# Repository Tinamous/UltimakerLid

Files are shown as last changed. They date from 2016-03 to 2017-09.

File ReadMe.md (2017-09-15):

#Ultimaker 2 Lid.

An acrylic lid for the Ultimaker 2, 2+ and Extended to help keep dust off the printer bead and maintain a more stable thermal environment.

#### V1.1 Lid:

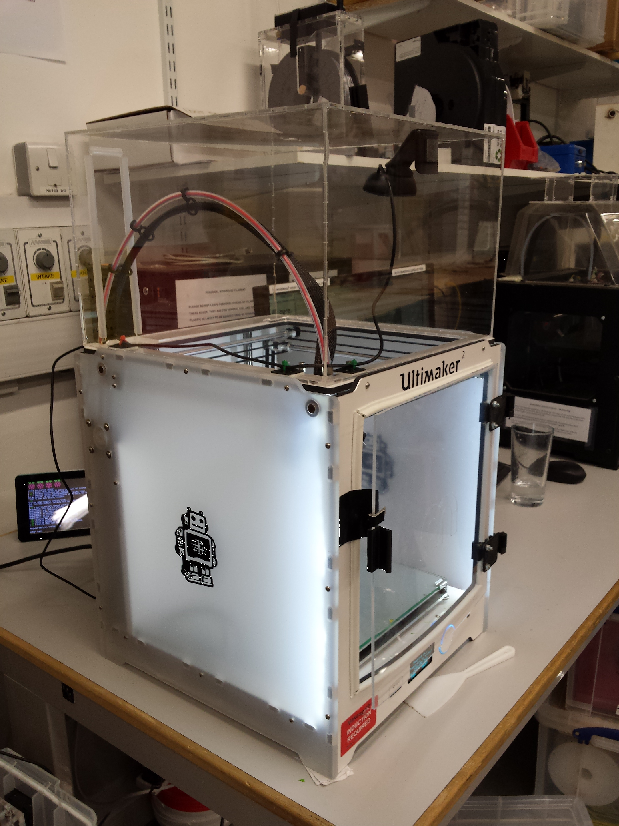
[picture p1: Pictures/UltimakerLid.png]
Ultimaker 2 Lid V1.1


#### V1.2 Lid:

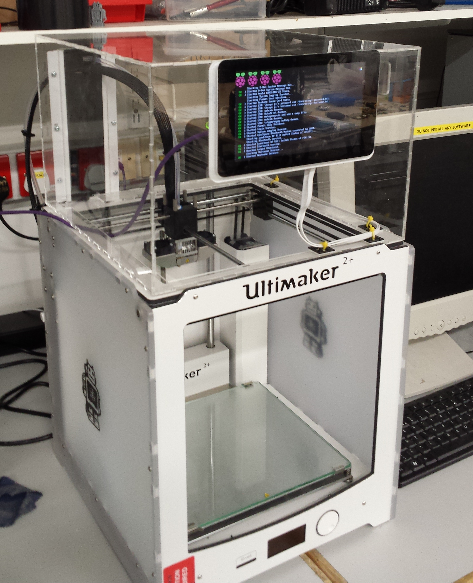
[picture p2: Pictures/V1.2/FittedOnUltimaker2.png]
Ultimaker 2 Lid V1.2


* Use 3mm Acrylic.
  * Use clear if you want to see your print when the lid is fitted
  * Suggest using cast acrylic to reduce internal forces in sheets.
* Laser cutting guides are for 600x400 sheets.
* Use Tensol 12 glue to glue the lid together.

### Versions:

* V1.0: Initial version - ignore this.
* V1.1: First built version. Option for hole in the top to allow mounting of camera.
* V1.2: Features a larger opening at the back to allow 2x draft excluder brush sets to be added and an opening at the front for the Raspberry Pi 7" Touch screen.
* V1.2.1: Do no use - Builds on V1.2 but is 40mm higher which makes better use of the acrylic when in 600x400 sheets. Appears Pi Display design changed.
* V1.2.2: Builds on V1.2.1 with better cutout for Pi Display, 40mm fan for pi cooling, 80 or 120mm fan cutouts at back.

V1.2.2 is the best option. However if you don't want the Pi Display mount on the front remove this in Inkscape or the laser cutter software.

Draft excluder used is Wickes "Brush Draught Excluder" - White PVCu. Product Id:218004 (http://www.wickes.co.uk/Wickes-Door-Brush-Draught-Excluder-White-838mm/p/218004)

V1.1 has a smaller opening for the Ultimaker boden tube and cables, if you don't want to use the draft excluder this version is better. Use the base of V1.1 as well as the opening is a different size.

If you don't use the draft excluded version cover the sharp edges where the boden tube goes through to prevent damadge. Some 6-8mm pipe the of the same material used for the boden tube, split along the length makes for a great cover.

### Lid Size: 

Width: 322mm
Height: 220mm (240mm for V1.2.1 and V1.2.2)
Depth: 335mm

## Assembly:

Glue: Use Tensol 12. http://www.rapidonline.com/pdf/87-2330U.PDF

Glue only in a well ventilated area. Don't spend too long in the area. 

Store the glue in the fridge for 24 hours before use and keep refrigerated between use, this increases the viscosity of the glue and makes it easier to work with.

The lid is glued in 4 stages with a 3 hour gap between each stage to allow the glue to set.

Black electrical tape is used to hold the box together when gluing, this works well as it's easily removed and can be stretched over corners to help keep the joints tight.

### Prep:

* You may wish to anneal the acrylic first to reduce the risk of cracking when glued. (See: https://en.wikipedia.org/wiki/Poly(methyl_methacrylate))
  * If using cast acrylic this may not be such an issue as the inner forces of the acrylic are less.
* Cut ~32 x 4-6 inch pieces of electrical tape ready to hold the box panels in place.
* Remove the all protective covering off all the pieces, you don't want that glued into your lid.
* Ensure you have a clean flat working surface and kitchen towel or similar to wipe up any dripped glue.
* Glue will run through the lid joints onto the work bench. Working on a paper cover will result in the paper being stuck to the lid, use wood as the work top (suggest not kitchen work top!)

When gluing:

* Don't apply too much glue.
* A 1-2mm bead size is ample. This will get drawn into the joint and give a high glue surface area.
* Try to get glue only where it is needed otherwise it eats into the finished surface and looks horrible. (i.e. don't dribble)
* Don't let the glue dispenser warm to much as the glue becomes very runny and is difficult to work with very quickly. Always return the glue to the fridge.
* You may wish to move the lid slightly every now and then shortly after gluing to remove any excess glue of the surface the lid is sitting on. Don't wipe the lid through as this will smear glue over it and look horrible.

### Assembly:

#### Phase 1 - Glue the bottom on:

* Place the lid base (the piece with the large hole in from sheet 3) on a flat surface with the back opening at the back left as it would be when fitted on the printer.
* Put 2 pieces of electrical tape on the bottom of the base piece on each side coming out about 3 inches ready to connect to a side/front/back panel.
* Place the back panel on ensuring the large hole matches up with the cut out on the base and is on the left hand side. This allows the cable/boden tube to go through the lid into the ultimaker. 
* Pull the tape tight and press against the back panel.
* Place a side panel onto one side, hold in place with the tape from the base, also add 2 pieces of tape along the back panel to side panel edge to hold them tight
* Repeat for the other side.
* Repeat for the front panel ensuring the cutout for the Pi Display is at the top, finally taping the front panel to the two side panels.
* The box should now be in a good shape and look almost as it would sat on the printer, held together sturdily with the electrical tape. Do not fit the lid yet
* Run a bead of Tensol 12 glue along the connecting 4 edges of the base (front/back and sides). 
* Do not glue up the edges at this stage as the glue will run down and form a big blob in the corner.
* Fit the top now to ensure the whole thing is square whist the glue sets. Ensure there is no glue around the top so it doesn't stick.
* Return glue bottle to fridge.
* Put kettle on and make a nice cup of tea.
* Wait for 3 hours for the glue to set.

#### Phase 2 - Glue one side:

* Rotate the lid 180 degrees so the back panel is nearest to you.
* Flip forwards so the top is now facing you and the back panel is laying flat on the bench.
* Remove the top.
* Run a bead of glue along both the mating edges of the back and side panels (should be horizontal on the bench now). 
  * Run the glue from the furthest away point stopping 20mm before getting to the lid top (i.e. going from lid bottom to top)
  * Be sure not to glue all the way to the lid top to prevent risk of gluing the top on at this stage.
* Return glue bottle to fridge. 
* Provided there is no glue near the lid connection you may wish to put the lid on to help keep the box square, suggest waiting a bit to let the glue spread first to ensure it won't creep into the top of the lid.
* Put kettle on and make a nice cup of tea.
* Wait for 3 hours for the glue to set.

#### Phase 3 - Glue the other side:

* Rotate the box 180 degrees so the last glued edge is now in the air and the remaining two side unglued edged are flat on the bench. Remove the lid if fitted.
* Repeat gluing as above, run a bead of glue from the back to the front along the side edges stopping 20 mm before the lid.
* Return glue bottle to fridge and again wait for the glue to start to set so it is no longer moving and fit the lid if you wish.
* Put kettle on and make a nice cup of tea.
* Wait for 3 hours to allow glue to set.

#### Phase 4 - Glue the top:

* Ensure that the top if fitted squarely, add some electrical tape top hold it in place against the sides/back/front.
* Rotate the lid forward so the lid top is now flat on the bench.
* You can now glue the 4 edges of the top to the sides/front/back panels by putting your hand through the large hole in the base panel.
  * Don't tilt the glue bottle when doing this otherwise you'll get glue on the inside of the lid top. Tilt the bottle only when about to glue the edges.
* Return glue bottle to fridge and wait 3 hours for the glue to set.
* Remove the electrical tape.
* Put kettle on and make a nice cup of tea you certainly deserve one now!

The glue should fully harden in 3 weeks, however it is usable once the final 3 hour wait is over. 

Hardening to reduce the 3 weeks can be speeded up by heating AFTER 24 hours, refer to the glue instructions for details on this.

#### Phase 5:

##### Draft excluder brushes

* Cut 2 lengths of draft excluder brush to fit the rear gap. 
  * Try to cut it so that one of the holes in the draft excluder lines up with a hole in the acrylic otherwise it will look odd
  * The brush should sit on the outside of the back of the lid with the fat part sitting in the gap towards the inside of the lid, this provides protection against the sharp edges of the lid for the moving cables and boden tube
* Mark then drill the other 2 holes in each brush of the draft excluder.
* You may wish to crimp the lower end of each brush to stop the bristles coming out now it's been cut.
* Fit both brushes using M3 machine screws, bolts and washers.

##### 7" Pi Display

* Cut 2x outlines from 3mm acrylic for the display (see V1.2 files).
  * If using V1.2 this may well come out of the offcuts from the back and front panel and the base panel.
* Attach the Pi Display PCB onto the display and connect up the flex cables
* Attach the display PCB to Pi flex cable (do not connect to the Pi at this time)
* Attach the 5v & GND cables to the display PCB
* Plug the Micro USB cable into the display PCB
** If using a Pi 3 with WiFi the voltage drop on the USB cable may be to large so use 2x USB cables, one for the Pi and one for the display and link only the GND connection
* Fit the smaller acrylic display mount first to the display
* Fit the slightly larger one next (this gives a stepped impression around the bottom and sides of the display
  * Ensure the cut out on the inside is at the bottom where the flex cable is.
  * No need to glue these, they are held in place by the display.
* Offer the display to the front of the lid carefully feeding in the USB, and interconnect cables.
  * The display flex cables go at the bottom and the display pcb to pi interconnect flex on the right hand side.
* Mound the display to the lid using M3 machine screws and washers on the inside to spread the load of the forces (don't over tighten) - suggest nylon bolts.
* Mount the Pi onto the display as you would do normally.
* Run the power cable to the bottom of the lid and around the edge to the right and hold in place with sticky feet and cable ties (ensure it won't get snagged with the printer head).
* Take the USB cable out of the lid via the small hole at the back right (V1.2+ only)
* Don't fix the cable to the ultimaker as this will hinder you removing the lid.
* Optionally include Ethernet cable if you're not using Wi-Fi
* Optionally include a USB camera on the back of the lid to monitor the roll, run the USB cable for that with the power USB cable
* Optionally include a USB cable to go to the USB port on the Ultimaker
* Optionally include an internal USB camera. Mount this to the lid back/side/front/top as you like with sticky fixers.
* Optionally attach a Pi Camera and mount that as desired.
* Optionally attach a Pi Hat to light up or monitor the temperature/humidity inside the lid.
* Optionally run OctoPi/OctoPrint on the Pi (NB: This doesn't appear to work overly well with the printer, we use it only for webcam monitoring).

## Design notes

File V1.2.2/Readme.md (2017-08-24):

Same as V1.2.1 (Draft excluder at rear and Pi Display, 40mm higher to make better use of 600x400 acrylic sheet).

* Increased cutout for the Raspberry Pi Display as the fixings appear to have changed slightly and it was already tight to fit.
* Moved Pi display down a little
* Cutout in top for 40mm fan to cool Pi.
* Cutout at rear for 80 or 120mm fan to cool/filter printer environment
* Add hole for DC Power connector. (12mm)
* Bottom - added plates for fans to cover hole if required
* Bottom - reduced cutout for screw/boden cable exit so it doesn't cut through the back as well.

Right, Left are unchanged from V1.2.1

Use http://www.makercase.com/ to create laser cut plan from .json file.

40mm fan (Top)
--------------
Holes 32mm apart. (16 from center)
main hole 38mm

Use:
{"params":[161,309,37,1],"type":"roundHole"},
{"params":[145,293,4,2],"type":"roundHole"},
{"params":[145,325,4,3],"type":"roundHole"},
{"params":[177,325,4,4],"type":"roundHole"},
{"params":[177,293,4,5],"type":"roundHole"}

80mm fan (Back)
---------------
Holes 71mm apart. (35.5 from center)
main hole 75mm

Use:
{"params":[60,60,75,10],"type":"roundHole"},
{"params":[24.4,24.4,4.4,11],"type":"roundHole"},
{"params":[24.4,95.5,4.4,12],"type":"roundHole"},
{"params":[95.5,95.5,4.4,13],"type":"roundHole"},
{"params":[95.5,24.4,4.4,14],"type":"roundHole"}

Add also cutout on bottom to cover the hole if not in use.

120mm fan (Back)
----------------
Holes 105mm apart. (52.5 from center)
main hole 115mm

Use:
{"params":[80,80,115,15],"type":"roundHole"},
{"params":[27.5,27.5,4.4,16],"type":"roundHole"},
{"params":[27.5,132.5,4.4,17],"type":"roundHole"},
{"params":[132.5,132.5,4.4,18],"type":"roundHole"},
{"params":[132.5,27.5,4.4,19],"type":"roundHole"},

Add also cutout on bottom to cover the hole if not in use.

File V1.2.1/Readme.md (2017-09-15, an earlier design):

Do not use this design. It appears the Pi Display has changed slightly making the cutout not work well. V1.2.2 has a larger cutout and is down a little to give a better fit.

Same as V1.2 (Draft excluder at rear and Pi Display) but 40mm higher (to make better use of 600x400 acrylic sheet + give more stable zone at the top with lack of airflow

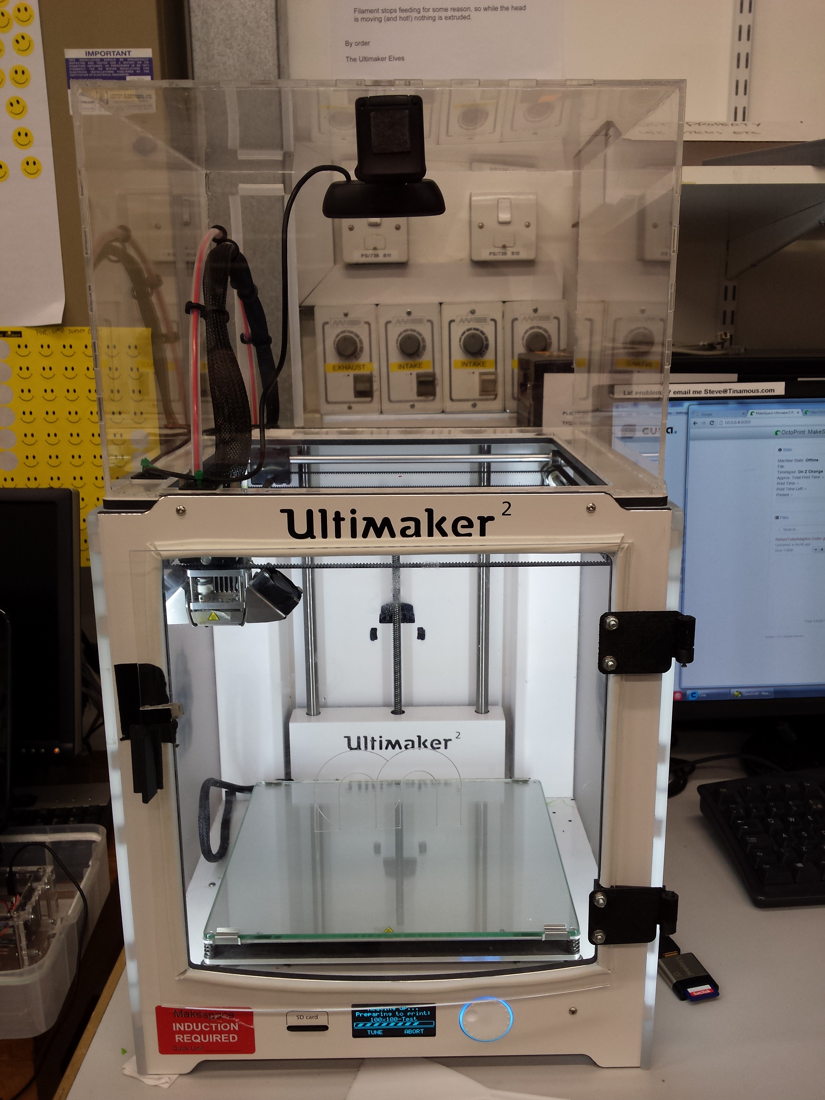
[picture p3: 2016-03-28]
Pictures/2015-11-13 16.56.00.jpg

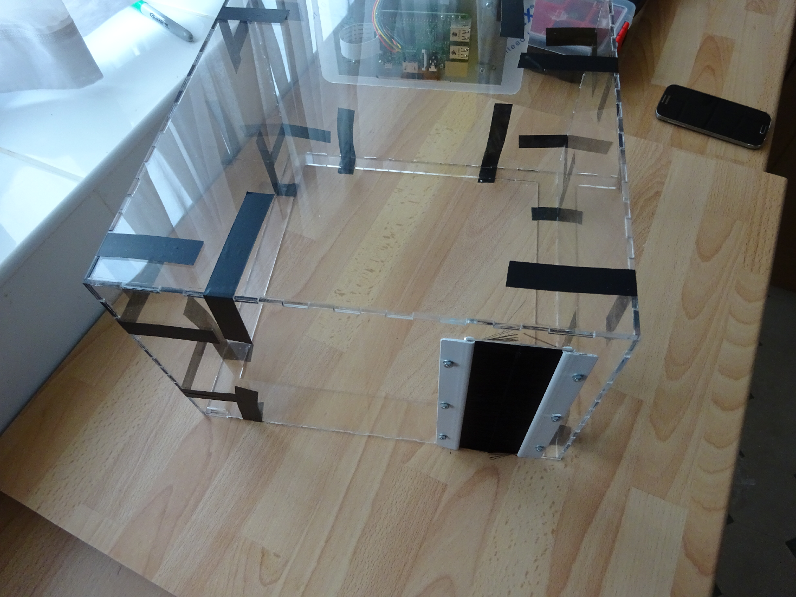
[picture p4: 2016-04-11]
Pictures/V1.2/RearBrushes.png

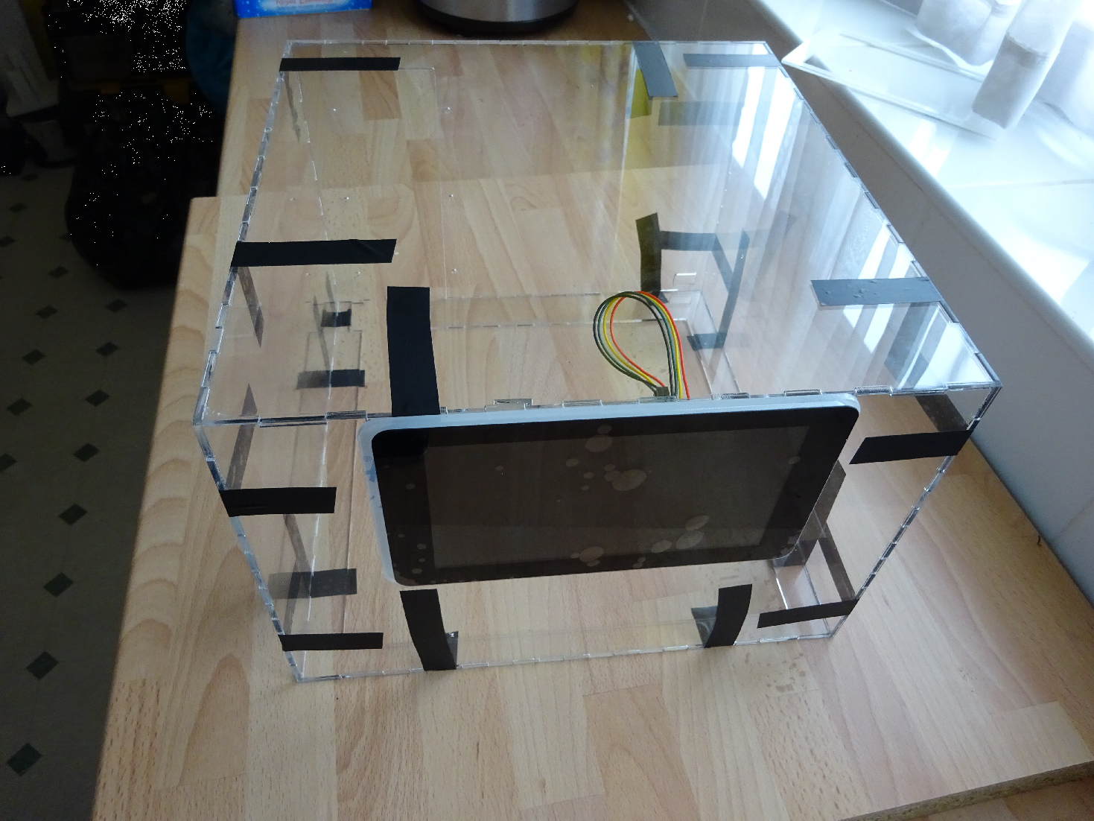
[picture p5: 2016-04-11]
Pictures/V1.2/PiDisplay.png

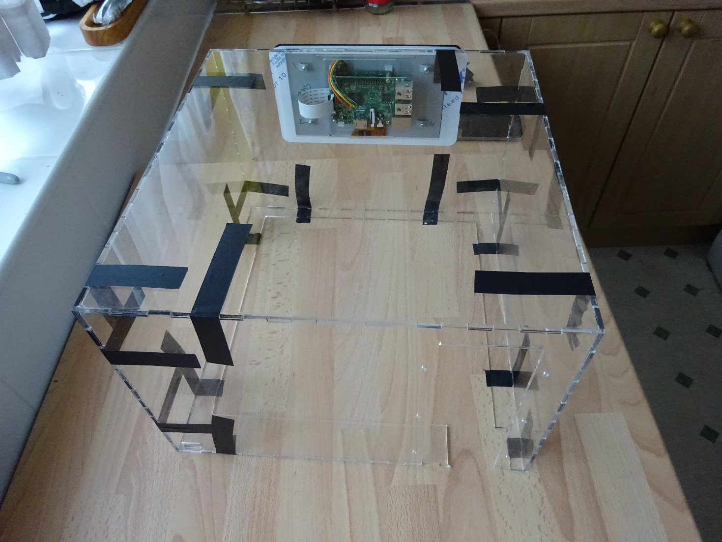
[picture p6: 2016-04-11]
Pictures/V1.2/PiDisplayRear.png

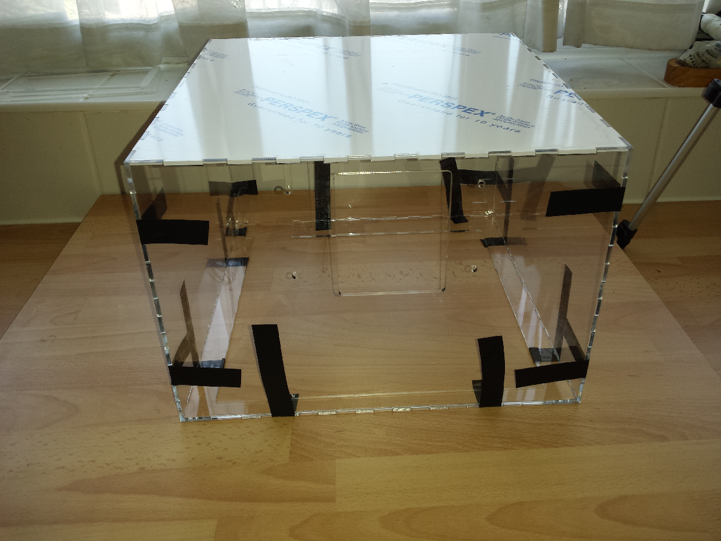
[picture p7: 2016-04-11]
Pictures/V1.2/GluingBase2.png

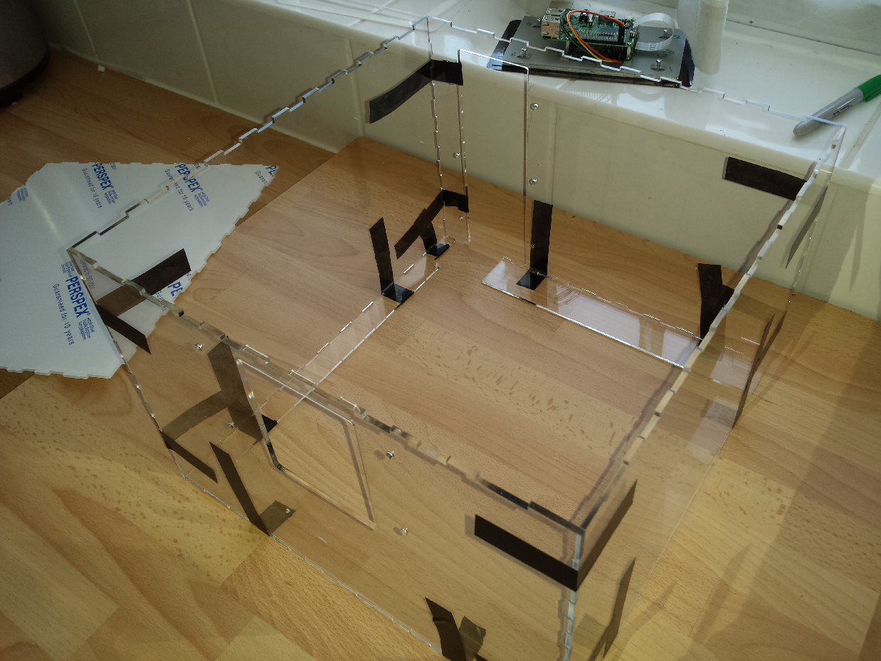
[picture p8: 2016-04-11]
Pictures/V1.2/GluingBase.png

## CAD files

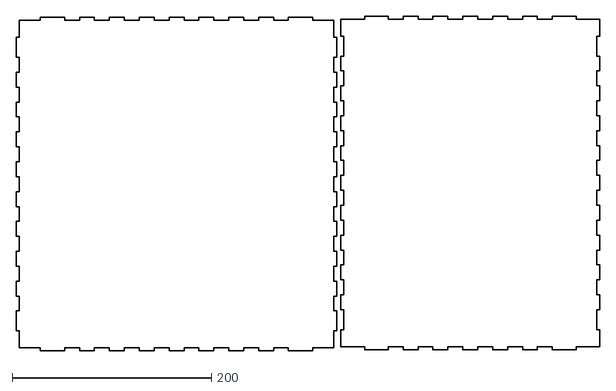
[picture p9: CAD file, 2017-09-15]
V1.2.2/TopAndSide-600x400-NoTopFan.dxf
586.2 x 336.2

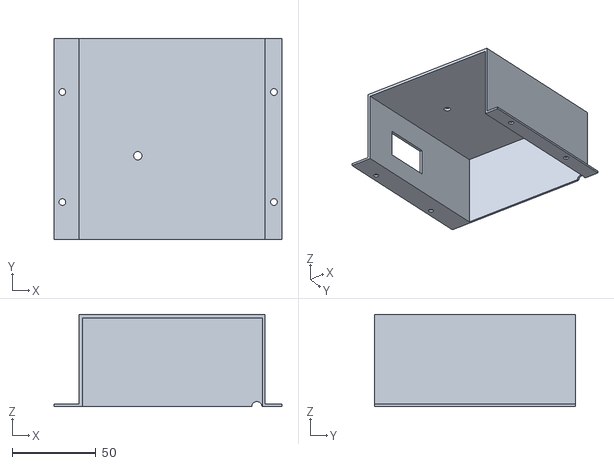
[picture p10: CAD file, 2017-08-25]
V1.2.2/PiCase.stl
136.0 x 120.0 x 55.0

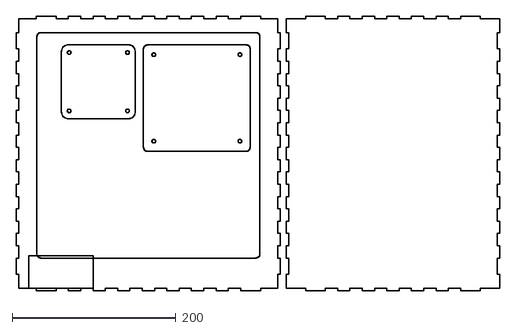
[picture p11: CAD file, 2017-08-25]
V1.2.2/BottomAndSide-600x400.dxf
589.3 x 335.0

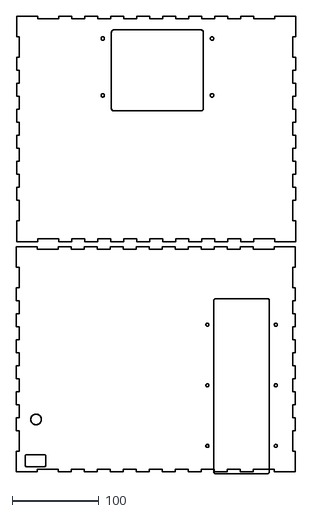
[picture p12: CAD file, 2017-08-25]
V1.2.2/BackAndFront-600x400-NoFan.dxf
322.3 x 528.0

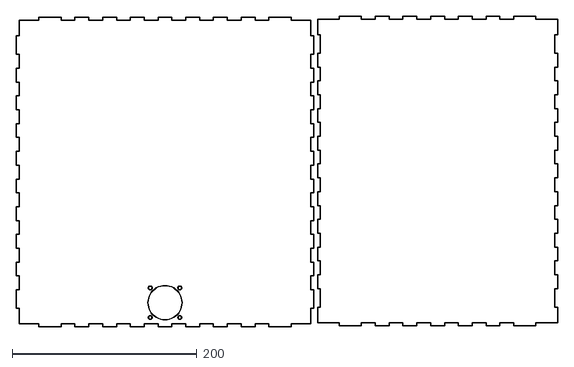
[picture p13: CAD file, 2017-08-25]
V1.2.2/TopAndSide-600x400.dxf
586.2 x 336.2

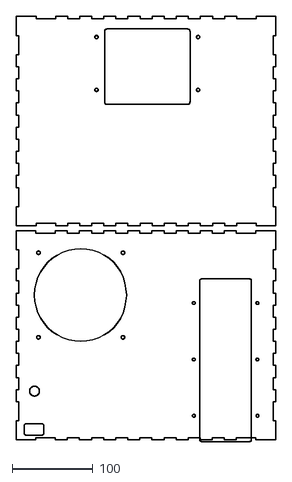
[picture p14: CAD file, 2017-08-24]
V1.2.2/BackAndFront-600x400-120Fan.dxf
322.3 x 528.0

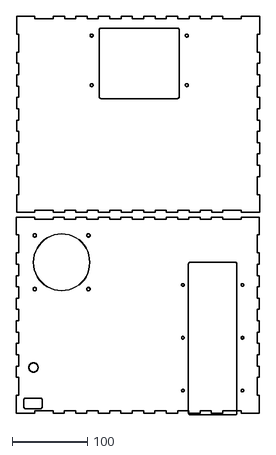
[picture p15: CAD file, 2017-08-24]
V1.2.2/BackAndFront-600x400-80Fan.dxf
322.3 x 528.0

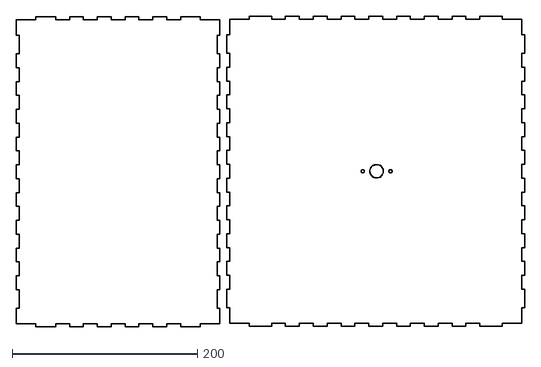
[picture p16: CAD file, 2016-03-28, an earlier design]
V1.1/lid-2b - TopWithCameraHoleAndSide.dxf
549.4 x 335.6

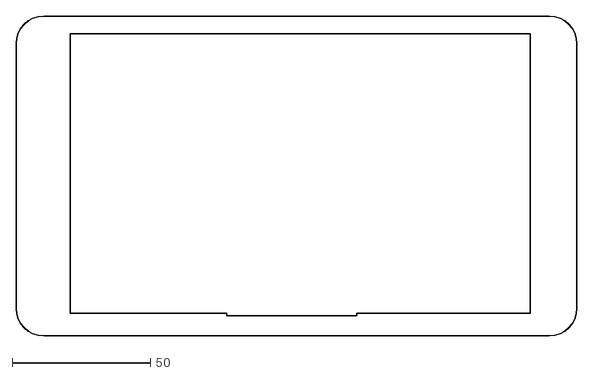
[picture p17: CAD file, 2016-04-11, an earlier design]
V1.2/DisplaySuround-2b.dxf
203.0 x 115.8

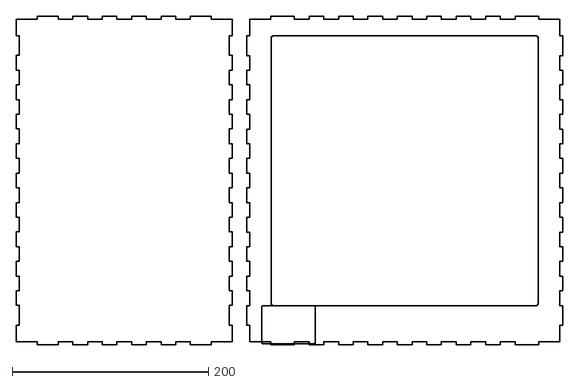
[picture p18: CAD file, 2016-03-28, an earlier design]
V1.1/lid-3 - BottomAndSide.dxf
556.9 x 335.1

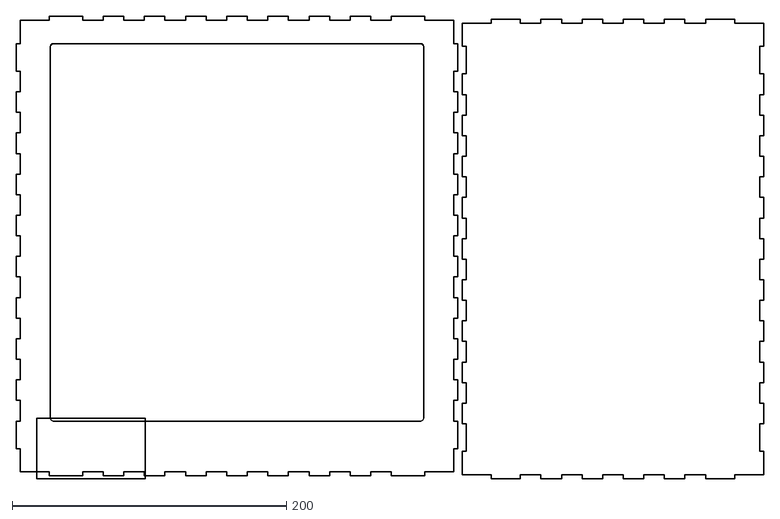
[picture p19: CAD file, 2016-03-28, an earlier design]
V1.2/BottomAndSide-600x400.dxf
545.0 x 337.0

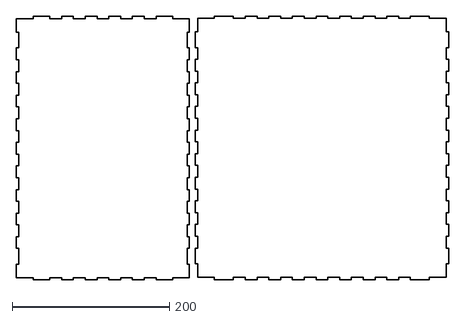
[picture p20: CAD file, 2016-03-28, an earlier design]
V1.1/lid-2a - TopNoHolesAndSide.dxf
549.4 x 335.6

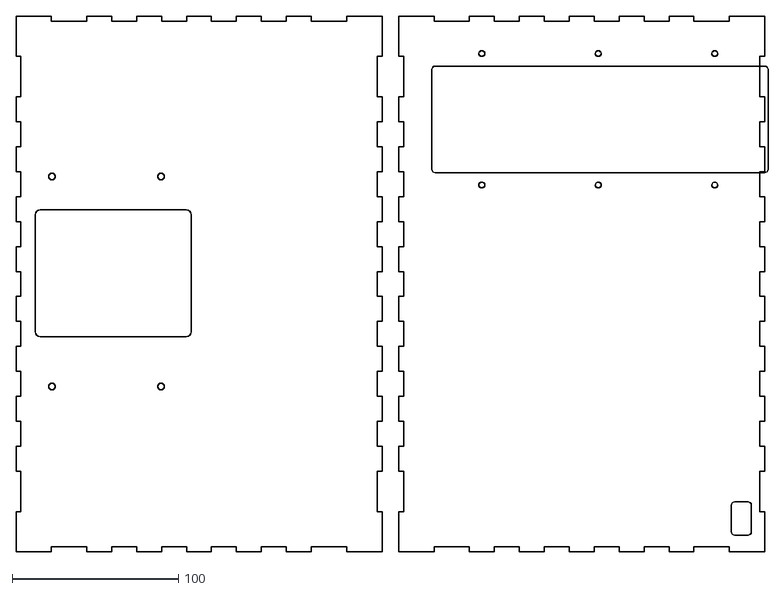
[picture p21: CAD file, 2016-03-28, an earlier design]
V1.2/BackAndFront-600x400.dxf
452.0 x 322.0

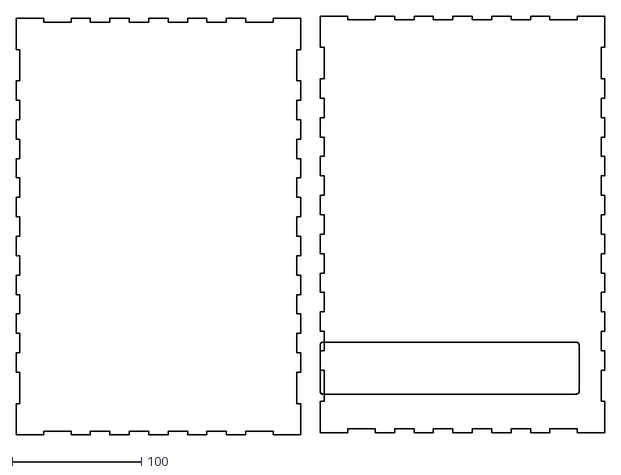
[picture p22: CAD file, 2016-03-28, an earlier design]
V1.1/lid-1 - BackAndFront.dxf
454.9 x 323.6

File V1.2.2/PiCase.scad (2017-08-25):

$fn = 60;

//{"params":[225.59,25.58,4,1],"type":"roundHole"},
//{"params":[225.59,91.23,4,2],"type":"roundHole"},
//{"params":[99.39,25.58,4,3],"type":"roundHole"},
//{"params":[99.39,91.23,4,4],"type":"roundHole"},
//{"params":[109.39,15.58,106.2,93.65,3,5],"type":"rectHole"}],

width = 136; // X
height = 120; // Y
depth = 55; // Z
// First hole y offset
// this is different between V1.2.1 and 1.2.2 cases
//holeYOffset = 21.58; // V1.2.1 - TODO: Check!
holeYOffset = 25.58; // V1.2.2

module PiModel() {
    translate([13+5, holeYOffset + 2, 13]) {
        cube([85, 60, 40]);
        
        // USB 
        translate([-20,0,1]) {
            cube([22,15, 18]);
        }
        
        // Second USB
        translate([-20,20,1]) {
            cube([22,15, 18]);
        }
        
        // Power connector
        translate([85,36,12]) {
            cube([15,12, 10]);
        }
    }
}

module baseLayer() {
    difference() {
        union() {
            // Base layer for holes.
            cube([width, height, 1.5]);
            
            translate([5 + 10, 0, -0]) {
                cube([width - 15 - 10, height, depth]);
            }
        }
        union() {
            // Drill the holess..
            // 5mm in, and 25.58mm down (from laser) - 3mm thickness acrylic + tollerance
            translate([5, holeYOffset- 3.2, -0.1]) {
                cylinder(d=4, h=2);
                translate([126.2, 0, 0]) {
                    #cylinder(d=4, h=2);
                }
                
                translate([126.2, 65.65, 0]) {
                    #cylinder(d=4, h=2);
                }
                
                translate([0, 65.65, 0]) {
                    #cylinder(d=4, h=2);
                }
            }
            
            // Cut out main Pi Body
            translate([5 + 12, -0.01, -0.1]) {
                cube([width - 17 - 11.5, height-1.5, depth-2]);
            }
            
            // Pi Offset (Y=0 = 27mm, X=13+5)
            // Cut out for the USB connectors
            translate([5 + 9 - 0.01, 26, 15]) {
                cube([4, 36, 20]);
            }
            
            // Cutout for the power cable.
            translate([width - 15, height +4, 0]) {
                rotate([90,0,0]) {
                    #cylinder(d=6, h=20);
                }
            }
            
            // Hole for temperature sensor.
            translate([50, 50, depth -10]) {
            
                #cylinder(d=5, h=20);
            }
                
        }
    }
}

baseLayer();
%PiModel();

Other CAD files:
V1.2/TopAndSide-600x400.dxf
V1.2/DisplaySuround-2.dxf
V1.2/DisplaySuround.dxf

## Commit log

2016-03-28 Initial commit.
    V1.1 Lid good.
    V1.2 Lid has 7" Pi display cut out and space for draft exluder brushes at rear exit.
    V1.2.1 Same as 1.2 but 40mm higher to make best use of 600x400 acrylic sheets, although missing USB cable exit.
    [BackAndFront-600x400.dxf, BottomAndSide-600x400.dxf, DisplaySuround-2.dxf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]
2016-04-11 Corrected wide display surround (2b) which was missing opject to path so had square corners.
    [DisplaySuround-2b.dxf]
2017-08-24 Added V1.2.2:
    Improved cutout for Pi Display.
    Added 40mm fan in top for Pi Cooling
    Added 80mm or 120mm fan at rear for post print cooling or to filter air when used with Active Charcoal filters.
    [BackAndFront-600x400-120Fan.dxf, BackAndFront-600x400-80Fan.dxf, BackAndFront-600x400-NoFan.dxf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]
2017-08-25 Renamed back/front with all fans to -AllFans and removed dxf as it's not one to cut.
    [BackAndFront-600x400.dxf]
2017-08-25 Regenerated dxf's after converting objects to paths.
    [BackAndFront-600x400-NoFan.dxf, BottomAndSide-600x400.dxf, TopAndSide-600x400.dxf]
2017-08-25 First attempt at a case to go over the Pi to allow cool air to be use on the Pi without going into the main case.
    [PiCase.scad, PiCase.stl]
2017-09-15 cutting dxf for top/side with no fan
    [TopAndSide-600x400-NoTopFan.dxf]
